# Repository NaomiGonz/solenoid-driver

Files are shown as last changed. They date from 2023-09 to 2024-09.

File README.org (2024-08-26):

** Single Channel Solenoid Driver

#+attr_org: :width 500px
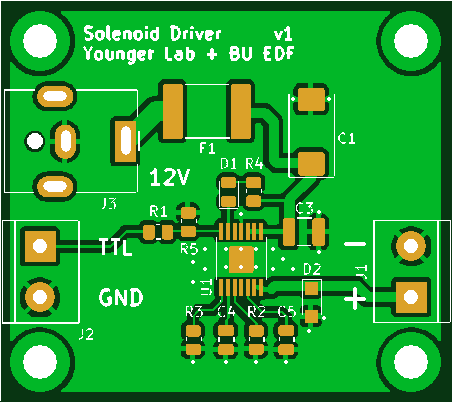
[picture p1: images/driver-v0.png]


A prototype single channel solenoid driver was developed for testing.

It is contained in the ~driver-v0~ folder.

We will have 3 manifolds with 8 of these in a row that need to be driven with 12V and signalled with a TTL line. All the manifolds will act in unison.

 - https://www.theleeco.com/product/lhd-series-2-way-control-solenoid-valve/
 - 3 boards, 8 channels each
 - 8 TTL inputs + GND
 - 8 12V outputs
 - 12V input on barrel jack
   - Plug:
     - https://www.digikey.com/en/products/detail/globtek-inc/CRP11856F00/16515770
     - Cable Assembly 2.1mm ID, 5.5mm OD Jack, Right Angle to Wire Leads Round 6.0' (1.83m)
   - Jack:
     - https://www.digikey.com/en/products/detail/cui-devices/PJ-063AH/2161208
     - PJ-063AH Power Barrel Connector Jack 2.10mm ID (0.083"), 5.50mm OD (0.217") Through Hole, Right Angle
 - LHDB1242115H
 - Spike+hold voltage: 12, 7.2
 - LOHM RATE** (Cv): 1500 Lohms (0.013)
 - Power Consumption At Hold Voltage (mW): 310
 - Response time: 10 ms Max

|----+-----------+-----+----------------------+--------------------+---------------------------|
|  # | Reference | Qty | Value                | PartNum            | Mfg                       |
|----+-----------+-----+----------------------+--------------------+---------------------------|
|  1 | C1        |   1 | 47uF                 | T491X476K035AT     | Kemet                     |
|  2 | C3        |   1 | 10uF                 | CL32A106KLULNNE    | Samsung Electro-Mechanics |
|  3 | C4        |   1 | 0.18 uF              | 08053C184KAT2A     | KYOCERA AVX               |
|  4 | C5        |   1 | 470pF                | C0805C471K5RAC7800 | Kemet                     |
|  5 | D1        |   1 | LED                  | 150080RS75000      | Wurth                     |
|  6 | D2        |   1 | PMEG10010ELRX        | PMEG10010ELRX      | Nexperia                  |
|  7 | F1        |   1 | 0ZCF0125FF2C         | 0ZCF0125FF2C       | Bel Fuse                  |
|  8 | J1, J2    |   2 | Screw_Terminal_01x02 | 282837-2           | TE                        |
|  9 | J3        |   1 | Barrel_Jack          | PJ-063AH           | CUI                       |
| 10 | R1        |   1 | 49R9                 | RC0805FR-0749R9L   | Yageo                     |
| 11 | R2        |   1 | 191k                 | RC0805FR-07191KL   | Yageo                     |
| 12 | R3        |   1 | 162k                 | RC0805FR-07162KL   | Yageo                     |
| 13 | R4, R5    |   2 | 4k7                  | RC0805JR-074K7L    | Yageo                     |
| 14 | U1        |   1 | DRV104PWP            | DRV104PWP          | TI                        |
|----+-----------+-----+----------------------+--------------------+---------------------------|

** Octal Channel Driver

** Dual Channel Complementary Driver

We will also have a pair of these valves that need to be driven by a single TTL
line in opposition (if one is in state A the other should be in state B).
 - LHDA1231415H
 - https://www.theleeco.com/product/lhd-series-3-way-control-solenoid-valve/
 - One TTL input  + GND
 - Two 12V complementary outputs

The solenoids should be driven with a high-side switch using a peak and hold circuit.

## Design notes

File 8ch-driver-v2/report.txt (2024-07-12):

Info: Processing symbol 'C1:Capacitor_Tantalum_SMD:CP_EIA-7343-43_Kemet-X_Pad2.25x2.55mm_HandSolder'.
Info: Processing symbol 'D39:LED_SMD:LED_0805_2012Metric'.
Info: Processing symbol 'C2:Capacitor_SMD:C_1210_3225Metric'.
Info: Processing symbol 'D10:Diode_SMD:Nexperia_CFP3_SOD-123W'.
Info: Processing symbol 'C3:Capacitor_SMD:C_1206_3216Metric'.
Info: Processing symbol 'Q2:Package_TO_SOT_SMD:SOT-23'.
Info: Processing symbol 'C4:Capacitor_SMD:C_1206_3216Metric'.
Info: Processing symbol 'D11:LED_SMD:LED_0805_2012Metric'.
Info: Processing symbol 'C5:Capacitor_SMD:C_1210_3225Metric'.
Info: Processing symbol 'D40:Diode_SMD:Nexperia_CFP3_SOD-123W'.
Info: Processing symbol 'C6:Capacitor_SMD:C_1206_3216Metric'.
Info: Processing symbol 'D12:LED_SMD:LED_0805_2012Metric'.
Info: Processing symbol 'C7:Capacitor_SMD:C_1206_3216Metric'.
Info: Processing symbol 'Q13:Package_TO_SOT_SMD:SOT-23'.
Info: Processing symbol 'C8:Capacitor_SMD:C_1210_3225Metric'.
Info: Processing symbol 'D13:Diode_SMD:Nexperia_CFP3_SOD-123W'.
Info: Processing symbol 'C9:Capacitor_SMD:C_1206_3216Metric'.
Info: Processing symbol 'D41:LED_SMD:LED_0805_2012Metric'.
Info: Processing symbol 'C10:Capacitor_SMD:C_1206_3216Metric'.
Info: Processing symbol 'D14:LED_SMD:LED_0805_2012Metric'.
Info: Processing symbol 'C11:Capacitor_SMD:C_1210_3225Metric'.
Info: Processing symbol 'Q3:Package_TO_SOT_SMD:SOT-23'.
Info: Processing symbol 'C12:Capacitor_SMD:C_1206_3216Metric'.
Info: Processing symbol 'D15:LED_SMD:LED_0805_2012Metric'.
Info: Processing symbol 'C13:Capacitor_SMD:C_1206_3216Metric'.
Info: Processing symbol 'D42:LED_SMD:LED_0805_2012Metric'.
Info: Processing symbol 'C14:Capacitor_SMD:C_1210_3225Metric'.
Info: Processing symbol 'D16:Diode_SMD:Nexperia_CFP3_SOD-123W'.
Info: Processing symbol 'C15:Capacitor_SMD:C_1206_3216Metric'.
Info: Processing symbol 'Q9:Package_TO_SOT_SMD:SOT-23'.
Info: Processing symbol 'C16:Capacitor_SMD:C_1206_3216Metric'.
Info: Processing symbol 'D17:LED_SMD:LED_0805_2012Metric'.
Info: Processing symbol 'C17:Capacitor_SMD:C_1210_3225Metric'.
Info: Processing symbol 'D43:Diode_SMD:Nexperia_CFP3_SOD-123W'.
Info: Processing symbol 'C18:Capacitor_SMD:C_1206_3216Metric'.
Info: Processing symbol 'D18:LED_SMD:LED_0805_2012Metric'.
Info: Processing symbol 'C19:Capacitor_SMD:C_1206_3216Metric'.
Info: Processing symbol 'Q4:Package_TO_SOT_SMD:SOT-23'.
Info: Processing symbol 'C20:Capacitor_SMD:C_1210_3225Metric'.
Info: Processing symbol 'D19:Diode_SMD:Nexperia_CFP3_SOD-123W'.
Info: Processing symbol 'C21:Capacitor_SMD:C_1206_3216Metric'.
Info: Processing symbol 'D44:LED_SMD:LED_0805_2012Metric'.
Info: Processing symbol 'C22:Capacitor_SMD:C_1206_3216Metric'.
Info: Processing symbol 'D20:LED_SMD:LED_0805_2012Metric'.
Info: Processing symbol 'C23:Capacitor_SMD:C_1210_3225Metric'.
Info: Processing symbol 'Q12:Package_TO_SOT_SMD:SOT-23'.
Info: Processing symbol 'C24:Capacitor_SMD:C_1206_3216Metric'.
Info: Processing symbol 'D21:LED_SMD:LED_0805_2012Metric'.
Info: Processing symbol 'C25:Capacitor_SMD:C_1206_3216Metric'.
Info: Processing symbol 'D45:LED_SMD:LED_0805_2012Metric'.
Info: Processing symbol 'C26:Capacitor_SMD:C_1210_3225Metric'.
Info: Processing symbol 'D22:Diode_SMD:Nexperia_CFP3_SOD-123W'.
Info: Processing symbol 'C27:Capacitor_SMD:C_1206_3216Metric'.
Info: Processing symbol 'Q5:Package_TO_SOT_SMD:SOT-23'.
Info: Processing symbol 'C28:Capacitor_SMD:C_1206_3216Metric'.
Info: Processing symbol 'D23:LED_SMD:LED_0805_2012Metric'.
Info: Processing symbol 'C29:Capacitor_SMD:C_1210_3225Metric'.
Info: Processing symbol 'D46:Diode_SMD:Nexperia_CFP3_SOD-123W'.
Info: Processing symbol 'C30:Capacitor_SMD:C_1206_3216Metric'.
Info: Processing symbol 'D24:LED_SMD:LED_0805_2012Metric'.
Info: Processing symbol 'C31:Capacitor_SMD:C_1206_3216Metric'.
Info: Processing symbol 'Q10:Package_TO_SOT_SMD:SOT-23'.
Info: Processing symbol 'C32:Capacitor_SMD:C_1210_3225Metric'.
Info: Processing symbol 'D25:Diode_SMD:Nexperia_CFP3_SOD-123W'.
Info: Processing symbol 'C33:Capacitor_SMD:C_1206_3216Metric'.
Info: Processing symbol 'D47:LED_SMD:LED_0805_2012Metric'.
Info: Processing symbol 'C34:Capacitor_SMD:C_1206_3216Metric'.
Info: Processing symbol 'D26:LED_SMD:LED_0805_2012Metric'.
Info: Processing symbol 'C35:Capacitor_SMD:C_1210_3225Metric'.
Info: Processing symbol 'Q6:Package_TO_SOT_SMD:SOT-23'.
Info: Processing symbol 'C36:Capacitor_SMD:C_1206_3216Metric'.
Info: Processing symbol 'D27:LED_SMD:LED_0805_2012Metric'.
Info: Processing symbol 'C37:Capacitor_SMD:C_1206_3216Metric'.
Info: Processing symbol 'D48:LED_SMD:LED_0805_2012Metric'.
Info: Processing symbol 'C38:Capacitor_SMD:C_1210_3225Metric'.
Info: Processing symbol 'D28:Diode_SMD:Nexperia_CFP3_SOD-123W'.
Info: Processing symbol 'C39:Capacitor_SMD:C_1206_3216Metric'.
Info: Processing symbol 'Q14:Package_TO_SOT_SMD:SOT-23'.
Info: Processing symbol 'C40:Capacitor_SMD:C_1206_3216Metric'.
Info: Processing symbol 'D29:LED_SMD:LED_0805_2012Metric'.
Info: Processing symbol 'C41:Capacitor_SMD:C_1210_3225Metric'.
Info: Processing symbol 'F1:Fuse:Fuse_2920_7451Metric'.
Info: Processing symbol 'C42:Capacitor_SMD:C_1206_3216Metric'.
Info: Processing symbol 'D30:LED_SMD:LED_0805_2012Metric'.
Info: Processing symbol 'C43:Capacitor_SMD:C_1206_3216Metric'.
Info: Processing symbol 'Q7:Package_TO_SOT_SMD:SOT-23'.
Info: Processing symbol 'C44:Capacitor_SMD:C_1210_3225Metric'.
Info: Processing symbol 'D31:Diode_SMD:Nexperia_CFP3_SOD-123W'.
Info: Processing symbol 'C45:Capacitor_SMD:C_1206_3216Metric'.
Info: Processing symbol 'H1:MountingHole:MountingHole_2.2mm_M2_Pad'.
Info: Processing symbol 'C46:Capacitor_SMD:C_1206_3216Metric'.
Info: Processing symbol 'D32:LED_SMD:LED_0805_2012Metric'.
Info: Processing symbol 'C47:Capacitor_SMD:C_1210_3225Metric'.
Info: Processing symbol 'Q16:Package_TO_SOT_SMD:SOT-23'.
Info: Processing symbol 'C48:Capacitor_SMD:C_1206_3216Metric'.
Info: Processing symbol 'D33:LED_SMD:LED_0805_2012Metric'.
Info: Processing symbol 'C49:Capacitor_SMD:C_1206_3216Metric'.
Info: Processing symbol 'H2:MountingHole:MountingHole_2.2mm_M2_Pad'.
Info: Processing symbol 'C50:Capacitor_SMD:C_1210_3225Metric'.
Info: Processing symbol 'D34:Diode_SMD:Nexperia_CFP3_SOD-123W'.
Info: Processing symbol 'C51:Capacitor_SMD:C_1210_3225Metric'.
Info: Processing symbol 'Q15:Package_TO_SOT_SMD:SOT-23'.
Info: Processing symbol 'D1:Diode_SMD:Nexperia_CFP3_SOD-123W'.
Info: Processing symbol 'D35:LED_SMD:LED_0805_2012Metric'.
Info: Processing symbol 'D2:LED_SMD:LED_0805_2012Metric'.
Info: Processing symbol 'J1:Connector_BarrelJack:BarrelJack_CUI_PJ-063AH_Horizontal'.
Info: Processing symbol 'D3:LED_SMD:LED_0805_2012Metric'.
Info: Processing symbol 'D36:LED_SMD:LED_0805_2012Metric'.
Info: Processing symbol 'D4:Diode_SMD:Nexperia_CFP3_SOD-123W'.
Info: Processing symbol 'Q11:Package_TO_SOT_SMD:SOT-23'.
Info: Processing symbol 'D5:LED_SMD:LED_0805_2012Metric'.
Info: Processing symbol 'D37:Diode_SMD:Nexperia_CFP3_SOD-123W'.
Info: Processing symbol 'D6:LED_SMD:LED_0805_2012Metric'.
Info: Processing symbol 'Q1:Package_TO_SOT_SMD:SOT-23'.
Info: Processing symbol 'D7:Diode_SMD:Nexperia_CFP3_SOD-123W'.
Info: Processing symbol 'D38:LED_SMD:LED_0805_2012Metric'.
Info: Processing symbol 'D8:LED_SMD:LED_0805_2012Metric'.
Info: Processing symbol 'Q8:Package_TO_SOT_SMD:SOT-23'.
Info: Processing symbol 'D9:LED_SMD:LED_0805_2012Metric'.
Info: Processing symbol 'R1:Resistor_SMD:R_1206_3216Metric'.
Info: Processing symbol 'R2:Resistor_SMD:R_1206_3216Metric'.
Info: Processing symbol 'R3:Resistor_SMD:R_1206_3216Metric'.
Info: Processing symbol 'R4:Resistor_SMD:R_1206_3216Metric'.
Info: Processing symbol 'R5:Resistor_SMD:R_1206_3216Metric'.
Info: Processing symbol 'R6:Resistor_SMD:R_1206_3216Metric'.
Info: Processing symbol 'R7:Resistor_SMD:R_1206_3216Metric'.
Info: Processing symbol 'R8:Resistor_SMD:R_1206_3216Metric'.
Info: Processing symbol 'R9:Resistor_SMD:R_1206_3216Metric'.
Info: Processing symbol 'R10:Resistor_SMD:R_1206_3216Metric'.
Info: Processing symbol 'R11:Resistor_SMD:R_1206_3216Metric'.
Info: Processing symbol 'R12:Resistor_SMD:R_1206_3216Metric'.
Info: Processing symbol 'R13:Resistor_SMD:R_1206_3216Metric'.
Info: Processing symbol 'R14:Resistor_SMD:R_1206_3216Metric'.
Info: Processing symbol 'R15:Resistor_SMD:R_1206_3216Metric'.
Info: Processing symbol 'R16:Resistor_SMD:R_1206_3216Metric'.
Info: Processing symbol 'R17:Resistor_SMD:R_1206_3216Metric'.
Info: Processing symbol 'R18:Resistor_SMD:R_1206_3216Metric'.
Info: Processing symbol 'R19:Resistor_SMD:R_1206_3216Metric'.
Info: Processing symbol 'R20:Resistor_SMD:R_1206_3216Metric'.
Info: Processing symbol 'R21:Resistor_SMD:R_1206_3216Metric'.
Info: Processing symbol 'R22:Resistor_SMD:R_1206_3216Metric'.
Info: Processing symbol 'R23:Resistor_SMD:R_1206_3216Metric'.
Info: Processing symbol 'R24:Resistor_SMD:R_1206_3216Metric'.
Info: Processing symbol 'R25:Resistor_SMD:R_1206_3216Metric'.
Info: Processing symbol 'R26:Resistor_SMD:R_1206_3216Metric'.
Info: Processing symbol 'R27:Resistor_SMD:R_1206_3216Metric'.
Info: Processing symbol 'R28:Resistor_SMD:R_1206_3216Metric'.
Info: Processing symbol 'R29:Resistor_SMD:R_1206_3216Metric'.
Info: Processing symbol 'R30:Resistor_SMD:R_1206_3216Metric'.
Info: Processing symbol 'R31:Resistor_SMD:R_1206_3216Metric'.
Info: Processing symbol 'R32:Resistor_SMD:R_1206_3216Metric'.
Info: Processing symbol 'R33:Resistor_SMD:R_1206_3216Metric'.
Info: Processing symbol 'R34:Resistor_SMD:R_1206_3216Metric'.
Info: Processing symbol 'R35:Resistor_SMD:R_1206_3216Metric'.
Info: Processing symbol 'R36:Resistor_SMD:R_1206_3216Metric'.
Info: Processing symbol 'R37:Resistor_SMD:R_1206_3216Metric'.
Info: Processing symbol 'R38:Resistor_SMD:R_1206_3216Metric'.
Info: Processing symbol 'R39:Resistor_SMD:R_1206_3216Metric'.
Info: Processing symbol 'R40:Resistor_SMD:R_1206_3216Metric'.
Info: Processing symbol 'R41:Resistor_SMD:R_1206_3216Metric'.
Info: Processing symbol 'R42:Resistor_SMD:R_1206_3216Metric'.
Info: Processing symbol 'R43:Resistor_SMD:R_1206_3216Metric'.
Info: Processing symbol 'R44:Resistor_SMD:R_1206_3216Metric'.
Info: Processing symbol 'R45:Resistor_SMD:R_1206_3216Metric'.
Info: Processing symbol 'R46:Resistor_SMD:R_1206_3216Metric'.
Info: Processing symbol 'R47:Resistor_SMD:R_1206_3216Metric'.
Info: Processing symbol 'R48:Resistor_SMD:R_1206_3216Metric'.
Info: Processing symbol 'R49:Resistor_SMD:R_1206_3216Metric'.
Info: Processing symbol 'R50:Resistor_SMD:R_1206_3216Metric'.
Info: Processing symbol 'R51:Resistor_SMD:R_1206_3216Metric'.
Info: Processing symbol 'R52:Resistor_SMD:R_1206_3216Metric'.
Info: Processing symbol 'R53:Resistor_SMD:R_1206_3216Metric'.
Info: Processing symbol 'R54:Resistor_SMD:R_1206_3216Metric'.
Info: Processing symbol 'R55:Resistor_SMD:R_1206_3216Metric'.
Info: Processing symbol 'R56:Resistor_SMD:R_1206_3216Metric'.
Info: Processing symbol 'R57:Resistor_SMD:R_1206_3216Metric'.
Info: Processing symbol 'R58:Resistor_SMD:R_1206_3216Metric'.
Info: Processing symbol 'R59:Resistor_SMD:R_1206_3216Metric'.
Info: Processing symbol 'R60:Resistor_SMD:R_1206_3216Metric'.
Info: Processing symbol 'R61:Resistor_SMD:R_1206_3216Metric'.
Info: Processing symbol 'R62:Resistor_SMD:R_1206_3216Metric'.
Info: Processing symbol 'R63:Resistor_SMD:R_1206_3216Metric'.
Info: Processing symbol 'R64:Resistor_SMD:R_1206_3216Metric'.
Info: Processing symbol 'R65:Resistor_SMD:R_1206_3216Metric'.
Info: Processing symbol 'R66:Resistor_SMD:R_1206_3216Metric'.
Info: Processing symbol 'R67:Resistor_SMD:R_1206_3216Metric'.
Info: Processing symbol 'R68:Resistor_SMD:R_1206_3216Metric'.
Info: Processing symbol 'R69:Resistor_SMD:R_1206_3216Metric'.
Info: Processing symbol 'R70:Resistor_SMD:R_1206_3216Metric'.
Info: Processing symbol 'R71:Resistor_SMD:R_1206_3216Metric'.
Info: Processing symbol 'R72:Resistor_SMD:R_1206_3216Metric'.
Info: Processing symbol 'R73:Resistor_SMD:R_1206_3216Metric'.
Info: Processing symbol 'R74:Resistor_SMD:R_1206_3216Metric'.
Info: Processing symbol 'R75:Resistor_SMD:R_1206_3216Metric'.
Info: Processing symbol 'R76:Resistor_SMD:R_1206_3216Metric'.
Info: Processing symbol 'R77:Resistor_SMD:R_1206_3216Metric'.
Info: Processing symbol 'R78:Resistor_SMD:R_1206_3216Metric'.
Info: Processing symbol 'R79:Resistor_SMD:R_1206_3216Metric'.
Info: Processing symbol 'R80:Resistor_SMD:R_1206_3216Metric'.
Info: Processing symbol 'R81:Resistor_SMD:R_1206_3216Metric'.
Info: Processing symbol 'R82:Resistor_SMD:R_1206_3216Metric'.
Info: Processing symbol 'R83:Resistor_SMD:R_1206_3216Metric'.
Info: Processing symbol 'R84:Resistor_SMD:R_1206_3216Metric'.
Info: Processing symbol 'R85:Resistor_SMD:R_1206_3216Metric'.
Info: Processing symbol 'R86:Resistor_SMD:R_1206_3216Metric'.
Info: Processing symbol 'R87:Resistor_SMD:R_1206_3216Metric'.
Info: Processing symbol 'R88:Resistor_SMD:R_1206_3216Metric'.
Info: Processing symbol 'R89:Resistor_SMD:R_1206_3216Metric'.
Info: Processing symbol 'R90:Resistor_SMD:R_1206_3216Metric'.
Info: Processing symbol 'R91:Resistor_SMD:R_1206_3216Metric'.
Info: Processing symbol 'R92:Resistor_SMD:R_1206_3216Metric'.
Info: Processing symbol 'R93:Resistor_SMD:R_1206_3216Metric'.
Info: Processing symbol 'R94:Resistor_SMD:R_1206_3216Metric'.
Info: Processing symbol 'R95:Resistor_SMD:R_1206_3216Metric'.
Info: Processing symbol 'R96:Resistor_SMD:R_1206_3216Metric'.
Info: Processing symbol 'U1:Solenoid_Driver:IC_TPS27S100BPWPR'.
Info: Processing symbol 'U2:Solenoid_Driver:IC_TPS27S100BPWPR'.
Info: Processing symbol 'U3:Solenoid_Driver:IC_TPS27S100BPWPR'.
Info: Processing symbol 'U4:Solenoid_Driver:IC_TPS27S100BPWPR'.
Info: Processing symbol 'U5:Solenoid_Driver:IC_TPS27S100BPWPR'.
Info: Processing symbol 'U6:Solenoid_Driver:IC_TPS27S100BPWPR'.
Info: Processing symbol 'U7:Solenoid_Driver:IC_TPS27S100BPWPR'.
Info: Processing symbol 'U8:Solenoid_Driver:IC_TPS27S100BPWPR'.
Info: Processing symbol 'U9:Solenoid_Driver:IC_TPS27S100BPWPR'.
Info: Processing symbol 'U10:Solenoid_Driver:IC_TPS27S100BPWPR'.
Info: Processing symbol 'U11:Solenoid_Driver:IC_TPS27S100BPWPR'.
Info: Processing symbol 'U12:Solenoid_Driver:IC_TPS27S100BPWPR'.
Info: Processing symbol 'U13:Solenoid_Driver:IC_TPS27S100BPWPR'.
Info: Processing symbol 'U14:Solenoid_Driver:IC_TPS27S100BPWPR'.
Info: Processing symbol 'U15:Solenoid_Driver:IC_TPS27S100BPWPR'.
Info: Processing symbol 'U16:Solenoid_Driver:IC_TPS27S100BPWPR'.
Info: Processing symbol 'U17:Package_TO_SOT_SMD:TO-252-2'.
Info: Processing symbol 'U18:FT4232H_FTD'.
Add Q14 (footprint 'Package_TO_SOT_SMD:SOT-23').
Add Q15 (footprint 'Package_TO_SOT_SMD:SOT-23').
Add Q16 (footprint 'Package_TO_SOT_SMD:SOT-23').
Add C1 (footprint 'Capacitor_Tantalum_SMD:CP_EIA-7343-43_Kemet-X_Pad2.25x2.55mm_HandSolder').
Add R1 (footprint 'Resistor_SMD:R_1206_3216Metric').
Add C2 (footprint 'Capacitor_SMD:C_1210_3225Metric').
Add R2 (footprint 'Resistor_SMD:R_1206_3216Metric').
Add C3 (footprint 'Capacitor_SMD:C_1206_3216Metric').
Add R3 (footprint 'Resistor_SMD:R_1206_3216Metric').
Add C4 (footprint 'Capacitor_SMD:C_1206_3216Metric').
Add R4 (footprint 'Resistor_SMD:R_1206_3216Metric').
Add C5 (footprint 'Capacitor_SMD:C_1210_3225Metric').
Add R5 (footprint 'Resistor_SMD:R_1206_3216Metric').
Add C6 (footprint 'Capacitor_SMD:C_1206_3216Metric').
Add R6 (footprint 'Resistor_SMD:R_1206_3216Metric').
Add C7 (footprint 'Capacitor_SMD:C_1206_3216Metric').
Add R7 (footprint 'Resistor_SMD:R_1206_3216Metric').
Add C8 (footprint 'Capacitor_SMD:C_1210_3225Metric').
Add R8 (footprint 'Resistor_SMD:R_1206_3216Metric').
Add C9 (footprint 'Capacitor_SMD:C_1206_3216Metric').
Add R9 (footprint 'Resistor_SMD:R_1206_3216Metric').
Add C10 (footprint 'Capacitor_SMD:C_1206_3216Metric').
Add R10 (footprint 'Resistor_SMD:R_1206_3216Metric').
Add C11 (footprint 'Capacitor_SMD:C_1210_3225Metric').
Add R11 (footprint 'Resistor_SMD:R_1206_3216Metric').
Add C12 (footprint 'Capacitor_SMD:C_1206_3216Metric').
Add R12 (footprint 'Resistor_SMD:R_1206_3216Metric').
Add C13 (footprint 'Capacitor_SMD:C_1206_3216Metric').
Add R13 (footprint 'Resistor_SMD:R_1206_3216Metric').
Add C14 (footprint 'Capacitor_SMD:C_1210_3225Metric').
Add R14 (footprint 'Resistor_SMD:R_1206_3216Metric').
Add C15 (footprint 'Capacitor_SMD:C_1206_3216Metric').
Add R15 (footprint 'Resistor_SMD:R_1206_3216Metric').
Add C16 (footprint 'Capacitor_SMD:C_1206_3216Metric').
Add R16 (footprint 'Resistor_SMD:R_1206_3216Metric').
Add C17 (footprint 'Capacitor_SMD:C_1210_3225Metric').
Add R17 (footprint 'Resistor_SMD:R_1206_3216Metric').
Add C18 (footprint 'Capacitor_SMD:C_1206_3216Metric').
Add R18 (footprint 'Resistor_SMD:R_1206_3216Metric').
Add C19 (footprint 'Capacitor_SMD:C_1206_3216Metric').
Add R19 (footprint 'Resistor_SMD:R_1206_3216Metric').
Add C20 (footprint 'Capacitor_SMD:C_1210_3225Metric').
Add R20 (footprint 'Resistor_SMD:R_1206_3216Metric').
Add C21 (footprint 'Capacitor_SMD:C_1206_3216Metric').
Add R21 (footprint 'Resistor_SMD:R_1206_3216Metric').
Add C22 (footprint 'Capacitor_SMD:C_1206_3216Metric').
Add R22 (footprint 'Resistor_SMD:R_1206_3216Metric').
Add C23 (footprint 'Capacitor_SMD:C_1210_3225Metric').
Add R23 (footprint 'Resistor_SMD:R_1206_3216Metric').
Add C24 (footprint 'Capacitor_SMD:C_1206_3216Metric').
Add R24 (footprint 'Resistor_SMD:R_1206_3216Metric').
Add C25 (footprint 'Capacitor_SMD:C_1206_3216Metric').
Add R25 (footprint 'Resistor_SMD:R_1206_3216Metric').
Add C26 (footprint 'Capacitor_SMD:C_1210_3225Metric').
Add R26 (footprint 'Resistor_SMD:R_1206_3216Metric').
Add C27 (footprint 'Capacitor_SMD:C_1206_3216Metric').
Add R27 (footprint 'Resistor_SMD:R_1206_3216Metric').
Add C28 (footprint 'Capacitor_SMD:C_1206_3216Metric').
Add R28 (footprint 'Resistor_SMD:R_1206_3216Metric').
Add C29 (footprint 'Capacitor_SMD:C_1210_3225Metric').
Add R29 (footprint 'Resistor_SMD:R_1206_3216Metric').
Add C30 (footprint 'Capacitor_SMD:C_1206_3216Metric').
Add R30 (footprint 'Resistor_SMD:R_1206_3216Metric').
Add C31 (footprint 'Capacitor_SMD:C_1206_3216Metric').
Add R31 (footprint 'Resistor_SMD:R_1206_3216Metric').
Add C32 (footprint 'Capacitor_SMD:C_1210_3225Metric').
Add R32 (footprint 'Resistor_SMD:R_1206_3216Metric').
Add C33 (footprint 'Capacitor_SMD:C_1206_3216Metric').
Add R33 (footprint 'Resistor_SMD:R_1206_3216Metric').
Add C34 (footprint 'Capacitor_SMD:C_1206_3216Metric').
Add R34 (footprint 'Resistor_SMD:R_1206_3216Metric').
Add C35 (footprint 'Capacitor_SMD:C_1210_3225Metric').
Add R35 (footprint 'Resistor_SMD:R_1206_3216Metric').
Add C36 (footprint 'Capacitor_SMD:C_1206_3216Metric').
Add R36 (footprint 'Resistor_SMD:R_1206_3216Metric').
Add C37 (footprint 'Capacitor_SMD:C_1206_3216Metric').
Add R37 (footprint 'Resistor_SMD:R_1206_3216Metric').
Add C38 (footprint 'Capacitor_SMD:C_1210_3225Metric').
Add R38 (footprint 'Resistor_SMD:R_1206_3216Metric').
Add C39 (footprint 'Capacitor_SMD:C_1206_3216Metric').
Add R39 (footprint 'Resistor_SMD:R_1206_3216Metric').
Add C40 (footprint 'Capacitor_SMD:C_1206_3216Metric').
Add R40 (footprint 'Resistor_SMD:R_1206_3216Metric').
Add C41 (footprint 'Capacitor_SMD:C_1210_3225Metric').
Add R41 (footprint 'Resistor_SMD:R_1206_3216Metric').
Add C42 (footprint 'Capacitor_SMD:C_1206_3216Metric').
Add R42 (footprint 'Resistor_SMD:R_1206_3216Metric').
Add C43 (footprint 'Capacitor_SMD:C_1206_3216Metric').
Add R43 (footprint 'Resistor_SMD:R_1206_3216Metric').
Add C44 (footprint 'Capacitor_SMD:C_1210_3225Metric').
Add R44 (footprint 'Resistor_SMD:R_1206_3216Metric').
Add C45 (footprint 'Capacitor_SMD:C_1206_3216Metric').
Add R45 (footprint 'Resistor_SMD:R_1206_3216Metric').
Add C46 (footprint 'Capacitor_SMD:C_1206_3216Metric').
Add R46 (footprint 'Resistor_SMD:R_1206_3216Metric').
Add C47 (footprint 'Capacitor_SMD:C_1210_3225Metric').
Add R47 (footprint 'Resistor_SMD:R_1206_3216Metric').
Add C48 (footprint 'Capacitor_SMD:C_1206_3216Metric').
Add R48 (footprint 'Resistor_SMD:R_1206_3216Metric').
Add C49 (footprint 'Capacitor_SMD:C_1206_3216Metric').
Add R49 (footprint 'Resistor_SMD:R_1206_3216Metric').
Add C50 (footprint 'Capacitor_SMD:C_1210_3225Metric').
Add R50 (footprint 'Resistor_SMD:R_1206_3216Metric').
Add C51 (footprint 'Capacitor_SMD:C_1210_3225Metric').
Add R51 (footprint 'Resistor_SMD:R_1206_3216Metric').
Add D1 (footprint 'Diode_SMD:Nexperia_CFP3_SOD-123W').
Add R52 (footprint 'Resistor_SMD:R_1206_3216Metric').
Add D2 (footprint 'LED_SMD:LED_0805_2012Metric').
Add R53 (footprint 'Resistor_SMD:R_1206_3216Metric').
Add D3 (footprint 'LED_SMD:LED_0805_2012Metric').
Add R54 (footprint 'Resistor_SMD:R_1206_3216Metric').
Add D4 (footprint 'Diode_SMD:Nexperia_CFP3_SOD-123W').
Add R55 (footprint 'Resistor_SMD:R_1206_3216Metric').
Add D5 (footprint 'LED_SMD:LED_0805_2012Metric').
Add R56 (footprint 'Resistor_SMD:R_1206_3216Metric').
Add D6 (footprint 'LED_SMD:LED_0805_2012Metric').
Add R57 (footprint 'Resistor_SMD:R_1206_3216Metric').
Add D7 (footprint 'Diode_SMD:Nexperia_CFP3_SOD-123W').
Add R58 (footprint 'Resistor_SMD:R_1206_3216Metric').
Add D8 (footprint 'LED_SMD:LED_0805_2012Metric').
Add R59 (footprint 'Resistor_SMD:R_1206_3216Metric').
Add D9 (footprint 'LED_SMD:LED_0805_2012Metric').
Add R60 (footprint 'Resistor_SMD:R_1206_3216Metric').
Add D10 (footprint 'Diode_SMD:Nexperia_CFP3_SOD-123W').
Add R61 (footprint 'Resistor_SMD:R_1206_3216Metric').
Add D11 (footprint 'LED_SMD:LED_0805_2012Metric').
Add R62 (footprint 'Resistor_SMD:R_1206_3216Metric').
Add D12 (footprint 'LED_SMD:LED_0805_2012Metric').
Add R63 (footprint 'Resistor_SMD:R_1206_3216Metric').
Add D13 (footprint 'Diode_SMD:Nexperia_CFP3_SOD-123W').
Add R64 (footprint 'Resistor_SMD:R_1206_3216Metric').
Add D14 (footprint 'LED_SMD:LED_0805_2012Metric').
Add R65 (footprint 'Resistor_SMD:R_1206_3216Metric').
Add D15 (footprint 'LED_SMD:LED_0805_2012Metric').
Add R66 (footprint 'Resistor_SMD:R_1206_3216Metric').
Add D16 (footprint 'Diode_SMD:Nexperia_CFP3_SOD-123W').
Add R67 (footprint 'Resistor_SMD:R_1206_3216Metric').
Add D17 (footprint 'LED_SMD:LED_0805_2012Metric').
Add R68 (footprint 'Resistor_SMD:R_1206_3216Metric').
Add D18 (footprint 'LED_SMD:LED_0805_2012Metric').
Add R69 (footprint 'Resistor_SMD:R_1206_3216Metric').
Add D19 (footprint 'Diode_SMD:Nexperia_CFP3_SOD-123W').
Add R70 (footprint 'Resistor_SMD:R_1206_3216Metric').
Add D20 (footprint 'LED_SMD:LED_0805_2012Metric').
Add R71 (footprint 'Resistor_SMD:R_1206_3216Metric').
Add D21 (footprint 'LED_SMD:LED_0805_2012Metric').
Add R72 (footprint 'Resistor_SMD:R_1206_3216Metric').
Add D22 (footprint 'Diode_SMD:Nexperia_CFP3_SOD-123W').
Add R73 (footprint 'Resistor_SMD:R_1206_3216Metric').
Add D23 (footprint 'LED_SMD:LED_0805_2012Metric').
Add R74 (footprint 'Resistor_SMD:R_1206_3216Metric').
Add D24 (footprint 'LED_SMD:LED_0805_2012Metric').
Add R75 (footprint 'Resistor_SMD:R_1206_3216Metric').
Add D25 (footprint 'Diode_SMD:Nexperia_CFP3_SOD-123W').
Add R76 (footprint 'Resistor_SMD:R_1206_3216Metric').
Add D26 (footprint 'LED_SMD:LED_0805_2012Metric').
Add R77 (footprint 'Resistor_SMD:R_1206_3216Metric').
Add D27 (footprint 'LED_SMD:LED_0805_2012Metric').
Add R78 (footprint 'Resistor_SMD:R_1206_3216Metric').
Add D28 (footprint 'Diode_SMD:Nexperia_CFP3_SOD-123W').
Add R79 (footprint 'Resistor_SMD:R_1206_3216Metric').
Add D29 (footprint 'LED_SMD:LED_0805_2012Metric').
Add R80 (footprint 'Resistor_SMD:R_1206_3216Metric').
Add D30 (footprint 'LED_SMD:LED_0805_2012Metric').
Add R81 (footprint 'Resistor_SMD:R_1206_3216Metric').
Add D31 (footprint 'Diode_SMD:Nexperia_CFP3_SOD-123W').
Add R82 (footprint 'Resistor_SMD:R_1206_3216Metric').
Add D32 (footprint 'LED_SMD:LED_0805_2012Metric').
Add R83 (footprint 'Resistor_SMD:R_1206_3216Metric').
Add D33 (footprint 'LED_SMD:LED_0805_2012Metric').
Add R84 (footprint 'Resistor_SMD:R_1206_3216Metric').
Add D34 (footprint 'Diode_SMD:Nexperia_CFP3_SOD-123W').
Add R85 (footprint 'Resistor_SMD:R_1206_3216Metric').
Add D35 (footprint 'LED_SMD:LED_0805_2012Metric').
Add R86 (footprint 'Resistor_SMD:R_1206_3216Metric').
Add D36 (footprint 'LED_SMD:LED_0805_2012Metric').
Add R87 (footprint 'Resistor_SMD:R_1206_3216Metric').
Add D37 (footprint 'Diode_SMD:Nexperia_CFP3_SOD-123W').
Add R88 (footprint 'Resistor_SMD:R_1206_3216Metric').
Add D38 (footprint 'LED_SMD:LED_0805_2012Metric').
Add R89 (footprint 'Resistor_SMD:R_1206_3216Metric').
Add D39 (footprint 'LED_SMD:LED_0805_2012Metric').
Add R90 (footprint 'Resistor_SMD:R_1206_3216Metric').
Add D40 (footprint 'Diode_SMD:Nexperia_CFP3_SOD-123W').
Add R91 (footprint 'Resistor_SMD:R_1206_3216Metric').
Add D41 (footprint 'LED_SMD:LED_0805_2012Metric').
Add R92 (footprint 'Resistor_SMD:R_1206_3216Metric').
Add D42 (footprint 'LED_SMD:LED_0805_2012Metric').
Add R93 (footprint 'Resistor_SMD:R_1206_3216Metric').
Add D43 (footprint 'Diode_SMD:Nexperia_CFP3_SOD-123W').
Add R94 (footprint 'Resistor_SMD:R_1206_3216Metric').
Add D44 (footprint 'LED_SMD:LED_0805_2012Metric').
Add R95 (footprint 'Resistor_SMD:R_1206_3216Metric').
Add D45 (footprint 'LED_SMD:LED_0805_2012Metric').
Add R96 (footprint 'Resistor_SMD:R_1206_3216Metric').
Add D46 (footprint 'Diode_SMD:Nexperia_CFP3_SOD-123W').
Add U1 (footprint 'Solenoid_Driver:IC_TPS27S100BPWPR').
Add D47 (footprint 'LED_SMD:LED_0805_2012Metric').
Add U2 (footprint 'Solenoid_Driver:IC_TPS27S100BPWPR').
Add D48 (footprint 'LED_SMD:LED_0805_2012Metric').
Add U3 (footprint 'Solenoid_Driver:IC_TPS27S100BPWPR').
Add F1 (footprint 'Fuse:Fuse_2920_7451Metric').
Add U4 (footprint 'Solenoid_Driver:IC_TPS27S100BPWPR').
Add J1 (footprint 'Connector_BarrelJack:BarrelJack_CUI_PJ-063AH_Horizontal').
Add U5 (footprint 'Solenoid_Driver:IC_TPS27S100BPWPR').
Add Q1 (footprint 'Package_TO_SOT_SMD:SOT-23').
Add U6 (footprint 'Solenoid_Driver:IC_TPS27S100BPWPR').
Add Q2 (footprint 'Package_TO_SOT_SMD:SOT-23').
Add U7 (footprint 'Solenoid_Driver:IC_TPS27S100BPWPR').
Add Q3 (footprint 'Package_TO_SOT_SMD:SOT-23').
Add U8 (footprint 'Solenoid_Driver:IC_TPS27S100BPWPR').
Add Q4 (footprint 'Package_TO_SOT_SMD:SOT-23').
Add U9 (footprint 'Solenoid_Driver:IC_TPS27S100BPWPR').
Add Q5 (footprint 'Package_TO_SOT_SMD:SOT-23').
Add U10 (footprint 'Solenoid_Driver:IC_TPS27S100BPWPR').
Add Q6 (footprint 'Package_TO_SOT_SMD:SOT-23').
Add U11 (footprint 'Solenoid_Driver:IC_TPS27S100BPWPR').
Add Q7 (footprint 'Package_TO_SOT_SMD:SOT-23').
Add U12 (footprint 'Solenoid_Driver:IC_TPS27S100BPWPR').
Add Q8 (footprint 'Package_TO_SOT_SMD:SOT-23').
Add U13 (footprint 'Solenoid_Driver:IC_TPS27S100BPWPR').
Add Q9 (footprint 'Package_TO_SOT_SMD:SOT-23').
Add U14 (footprint 'Solenoid_Driver:IC_TPS27S100BPWPR').
Add Q10 (footprint 'Package_TO_SOT_SMD:SOT-23').
Add U15 (footprint 'Solenoid_Driver:IC_TPS27S100BPWPR').
Add Q11 (footprint 'Package_TO_SOT_SMD:SOT-23').
Add U16 (footprint 'Solenoid_Driver:IC_TPS27S100BPWPR').
Add Q12 (footprint 'Package_TO_SOT_SMD:SOT-23').
Add U17 (footprint 'Package_TO_SOT_SMD:TO-252-2').
Add Q13 (footprint 'Package_TO_SOT_SMD:SOT-23').
Add U18 (footprint 'FT4232H_FTD').
Warning: No net found for component H1 pad 1 (no pin 1 in symbol).
Warning: No net found for component H2 pad 1 (no pin 1 in symbol).

Info: Total warnings: 2, errors: 0.

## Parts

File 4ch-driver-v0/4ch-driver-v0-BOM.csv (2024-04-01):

Source: | /Users/naomi_12/Desktop/Research/Younger-Lab/solenoid-driver-master/4ch-driver-v0/4ch-driver-v0.kicad_sch
Date: | 2024 March 31, Sunday 21:11:15
Tool: | Eeschema 7.0.7
Generator: | /Applications/KiCad/KiCad.app/Contents/SharedSupport/plugins/bom_csv_grouped_by_value.py
Component Count: | 68
Collated Components:
Item | Qty | Reference(s) | Value | LibPart | Footprint | Datasheet | DNP | Mfg | PartNum | Sim.Device | Sim.Pins
1 | 1 | C1 | 47uF | Device:C_Polarized | Capacitor_Tantalum_SMD:CP_EIA-7343-43_Kemet-X_Pad2.25x2.55mm_HandSolder | ~ |  | Kemet | T491X476K035AT
2 | 4 | C2, C7, C11, C14 | 0.18uF | Device:C_Small | Capacitor_SMD:C_0805_2012Metric | ~ |  | KYOCERA AVX | 08053C184KAT2A
3 | 4 | C3, C8, C12, C15 | 470pF | Device:C_Small | Capacitor_SMD:C_0805_2012Metric | ~ |  | Kemet | C0805C471K5RAC7800
4 | 4 | C4, C9, C13, C16 | 10uF | Device:C | Capacitor_SMD:C_1210_3225Metric | ~ |  | Samsung Electro-Mechanics | CL32A106KLULNNE
5 | 4 | C5, C10, C17, C18 | 0.1uF | Device:C_Small | Capacitor_SMD:C_0805_2012Metric | ~ |  | KYOCERA AVX | 08053C184KAT2A
6 | 1 | C6 | 10uF | Device:C_Small | Capacitor_SMD:C_1210_3225Metric | ~ |  | KYOCERA AVX | 08053C184KAT2A
7 | 8 | D1, D2, D4, D5, D7, D9, D11, D12 | LED | Device:LED | LED_SMD:LED_0805_2012Metric | ~ |  | Wurth | 150080RS75000
8 | 4 | D3, D6, D8, D10 | PMEG10010ELRX | Device:D | Diode_SMD:Nexperia_CFP3_SOD-123W | ~ |  | Nexperia | PMEG10010ELRX | D | 1=K 2=A
9 | 1 | F1 | 0ZCF0125FF2C | Device:Polyfuse | Fuse:Fuse_2920_7451Metric | ~ |  | Bel Fuse | 0ZCF0125FF2C
10 | 1 | J1 | Barrel_Jack | Connector:Barrel_Jack | Connector_BarrelJack:BarrelJack_CUI_PJ-063AH_Horizontal | ~ |  | CUI | PJ-063AH
11 | 2 | J2, J3 | Screw_Terminal_01x04 | Connector:Screw_Terminal_01x04 | TerminalBlock:TerminalBlock_bornier-4_P5.08mm | ~
12 | 1 | J4 | Screw_Terminal_01x02 | Connector:Screw_Terminal_01x02 | TerminalBlock:TerminalBlock_bornier-2_P5.08mm | ~ |  | TE | 282837-2
13 | 4 | Q1, Q2, Q3, Q4 | 2N7002E | Transistor_FET:2N7002E | Package_TO_SOT_SMD:SOT-23 | http://www.diodes.com/assets/Datasheets/ds30376.pdf
14 | 4 | R1, R2, R7, R21 | 1K | Device:R_US | Resistor_SMD:R_0805_2012Metric | ~ |  | Yageo | RC0805FR-07162KL
15 | 8 | R3, R4, R8, R9, R10, R13, R16, R17 | 4k7 | Device:R_US | Resistor_SMD:R_0805_2012Metric | ~ |  | Yageo | RC0805JR-074K7L
16 | 4 | R5, R11, R14, R18 | 162k | Device:R_US | Resistor_SMD:R_0805_2012Metric | ~ |  | Yageo | RC0805FR-07162KL
17 | 4 | R6, R12, R15, R19 | 191k | Device:R_US | Resistor_SMD:R_0805_2012Metric | ~ |  | Yageo | RC0805FR-07191KL
18 | 1 | R20 | 49R9 | Device:R_US | Resistor_SMD:R_0805_2012Metric | ~ |  | Yageo | RC0805FR-0749R9L
19 | 4 | U1, U3, U5, U6 | DRV104PWP | DRV104PWP:DRV104PWP | Solenoid_Driver:IC_TPS27S100BPWPR |  |  | TI | DRV104PWP
20 | 1 | U2 | BD750L2FP3-CE2 | Regulator_Linear:BD750L2FP3-CE | Package_TO_SOT_SMD:SOT-223-3_TabPin2
21 | 2 | U4, U7 | SN74LVC2G125DCUR | Buffer:SN74LVC2G125 | Package_SO:VSSOP-8_2.3x2mm_P0.5mm
22 | 1 | U8 | SN74AHCT1G04DBVR | Inverters:SN74AHCT1G04 | Package_TO_SOT_SMD:SOT-23-5

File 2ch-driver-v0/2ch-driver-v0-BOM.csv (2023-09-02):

Source: | /Users/naomi_12/Desktop/Meg-Younger-Lab/solenoid-driver-master/2ch-driver-v0/2ch-driver-v0.kicad_sch
Date: | 2023 August 22, Tuesday 11:58:14
Tool: | Eeschema 7.0.7
Generator: | /Applications/KiCad/KiCad.app/Contents/SharedSupport/plugins/bom_csv_grouped_by_value.py
Component Count: | 38
Collated Components:
Item | Qty Per Board | Reference(s) | Value | LibPart | Footprint | Link to Buy | Mfg | PartNum | Qty to Order | Indv Price | Group Price
1 | 1 | C1 | 47uF | Device:C_Polarized | Capacitor_Tantalum_SMD:CP_EIA-7343-43_Kemet-X_Pad2.25x2.55mm_HandSolder | https://www.digikey.com/en/products/detail/kemet/T491X476K035AT/818681 | Kemet | T491X476K035AT | 10 | $2.33 | $23.28
2 | 2 | C2, C7 | 0.18uF | Device:C_Small | Capacitor_SMD:C_0805_2012Metric | https://www.digikey.com/en/products/detail/kyocera-avx/08053C184KAT2A/563508 | KYOCERA AVX | 08053C184KAT2A | 50 | $0.14 | $4.32
3 | 2 | C3, C8 | 470pF | Device:C_Small | Capacitor_SMD:C_0805_2012Metric | https://www.digikey.com/en/products/detail/kemet/C0805C471K5RAC7800/411141 | Kemet | C0805C471K5RAC7800 | 50 | $0.04 | $1.87
4 | 3 | C4, C9,C6 | 10uF | Device:C | Capacitor_SMD:C_1210_3225Metric | https://www.digikey.com/en/products/detail/samsung-electro-mechanics/CL32A106KLULNNE/3888965 | Samsung Electro-Mechanics | CL32A106KLULNNE | 50 | $0.17 | $8.49
5 | 2 | C5, C10 | 0.1uF | Device:C_Small | Capacitor_SMD:C_0805_2012Metric | https://www.digikey.com/en/products/detail/samsung-electro-mechanics/CL21B104KBCNNNC/3886661 | Samsung Electro-Mechanics | CL21B104KBCNNNC | 50 | $0.02 | $1.20
6 | 2 | D2, D5 | LED Red | Device:LED | LED_SMD:LED_0805_2012Metric | https://www.digikey.com/en/products/detail/wŸrth-elektronik/150080RS75000/4489918 | Wurth | 150080RS75000 | 50 | $0.18 | $8.80
7 | 2 | D1, D4 | LED Green | Device:LED | LED_SMD:LED_0805_2012Metric | https://www.digikey.com/en/products/detail/wŸrth-elektronik/150080VS75000/4489924 | Wurth | 150080VS75000 | 50 | $0.18 | $8.80
8 | 2 | D3, D6 | PMEG10010ELRX | Device:D | Diode_SMD:Nexperia_CFP3_SOD-123W | https://www.digikey.com/en/products/detail/nexperia-usa-inc/PMEG10010ELRX/5436248 | Nexperia | PMEG10010ELRX | 50 | $0.29 | $14.30
9 | 1 | F1 | 0ZCF0125FF2C | Device:Polyfuse | Fuse:Fuse_2920_7451Metric | https://www.digikey.com/en/products/detail/bel-fuse-inc/0ZCF0125FF2C/4156315 | Bel Fuse | 0ZCF0125FF2C | 10 | $0.28 | $2.84
10 | 1 | J1 | Barrel_Jack | Connector:Barrel_Jack | Connector_BarrelJack:BarrelJack_CUI_PJ-063AH_Horizontal | https://www.digikey.com/en/products/detail/cui-devices/PJ-063AH/2161208 | CUI | PJ-063AH | 25 | $1.27 | $31.85
11 | 3 | J2, J3, J5 | Screw_Terminal_01x02 | Connector:Screw_Terminal_01x02 | TerminalBlock:TerminalBlock_bornier-2_P5.08mm | https://www.digikey.com/en/products/detail/te-connectivity-amp-connectors/282837-2/2187973 | TE | 282837-2 | 25 | $0.68 | $16.95
12 | 2 | Q1, Q2 | 2N7002E | Transistor_FET:2N7002E | Package_TO_SOT_SMD:SOT-23 | https://www.digikey.com/en/products/detail/diodes-incorporated/ZXMN2B01FTA/1557727 | Diodes Inc | ZXMN2B01FTA | 10 | $0.37 | $3.74
13 | 2 | R1, R7 | 1K | Device:R_US | Resistor_SMD:R_0805_2012Metric | https://www.digikey.com/en/products/detail/yageo/RC0805FR-071KL/727444 | Yageo | RC0805FR-071KL | 50 | $0.02 | $0.76
14 | 1 | R2 | 49R9 | Device:R_US | Resistor_SMD:R_0805_2012Metric | https://www.digikey.com/en/products/detail/yageo/RC0805FR-0749R9L/727984 | Yageo | RC0805FR-0749R9L | 10 | $0.02 | $0.24
15 | 4 | R3, R4, R9, R10 | 4k7 | Device:R_US | Resistor_SMD:R_0805_2012Metric | https://www.digikey.com/en/products/detail/yageo/RC0805JR-074K7L/728327 | Yageo | RC0805JR-074K7L | 50 | $0.01 | $0.68
16 | 2 | R5, R11 | 162k | Device:R_US | Resistor_SMD:R_0805_2012Metric | https://www.digikey.com/en/products/detail/yageo/RC0805FR-07162KL/727630 | Yageo | RC0805FR-07162KL | 50 | $0.02 | $0.76
17 | 2 | R6, R12 | 191k | Device:R_US | Resistor_SMD:R_0805_2012Metric | https://www.digikey.com/en/products/detail/yageo/RC0805FR-07191KL/727660 | Yageo | RC0805FR-07191KL | 50 | $0.02 | $0.77
18 | 2 | U1, U3 | DRV104PWP | DRV104PWP:DRV104PWP | Solenoid_Driver:IC_TPS27S100BPWPR | https://www.digikey.com/en/products/detail/texas-instruments/DRV104PWP/1509554 | TI | DRV104PWP | 25 | $4.55 | $113.74
19 | 1 | U2 | ~ | Regulator_Linear:BD750L2FP3-CE | Package_TO_SOT_SMD:SOT-223-3_TabPin2 | https://www.digikey.com/en/products/detail/rohm-semiconductor/BD750L2FP3-CE2/4625570 | Rohm | BD750L2FP3-CE2 | 10 | $1.54 | $15.39
20 | 1 | U4 | ~ | Inverters:SN74AHCT1G04 | Package_TO_SOT_SMD:SOT-23-5 | https://www.digikey.com/en/products/detail/texas-instruments/SN74AHCT1G04DBVR/276756 | Texas Instr | SN74AHCT1G04DBVR | 10 | $0.27 | $2.69
 |  |  |  |  |  |  |  |  |  | TOTAL: | $261.47
 | Digikey Cart: | https://www.digikey.com/short/47vpb32n

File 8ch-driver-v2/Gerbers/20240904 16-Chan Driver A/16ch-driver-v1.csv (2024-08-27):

Id | Designator | Footprint | Quantity | Designation | Supplier and ref
1 | R23,R11,R35,R29,R47,R5,R17,R41,R59,R71,R77,R65,R89,R95,R83,R53 | R_1206_3216Metric | 16 | 191k
2 | C3,C6,C18,C12,C24,C9,C21,C15,C27,C39,C30,C45,C42,C36,C33,C48 | C_1206_3216Metric | 16 | 0.18uF
3 | R16,R40,R37,R19,R28,R48,R4,R46,R30,R1,R34,R43,R10,R6,R7,R18,R24,R13,R42,R12,R31,R22,R36,R25,R78,R55,R67,R60,R70,R76,R90,R61,R94,R85,R64,R84,R54,R49,R73,R72,R66,R96,R91,R58,R52,R82,R79,R88 | R_1206_3216Metric | 48 | 4k7
4 | C23,C11,C14,C17,C2,C20,C5,C8,C38,C32,C35,C29,C26,C41,C47,C44 | C_1210_3225Metric | 16 | 10uF
5 | D33,D42,D39,D24,D27,D45,D3,D9,D30,D18,D15,D21,D48,D36,D12,D6 | LED_0805_2012Metric | 16 | LED
6 | C4,C16,C13,C19,C7,C25,C22,C10,C49,C40,C37,C31,C43,C46,C34,C28 | C_1206_3216Metric | 16 | 470pF
7 | D38,D29,D5,D41,D11,D26,D23,D47,D44,D20,D2,D14,D8,D32,D35,D17 | LED_0805_2012Metric | 16 | LED Green
8 | H3,H1,H2,H4 | MountingHole_3.2mm_M3 | 4 | MountingHole
9 | R3,R9,R33,R45,R39,R15,R27,R21,R57,R63,R69,R75,R93,R51,R81,R87 | R_1206_3216Metric | 16 | 49R9
10 | U3,U8,U1,U2,U5,U4,U6,U7,U12,U13,U9,U16,U10,U14,U15,U11 | IC_TPS27S100BPWPR | 16 | DRV104PWP
11 | D13,D22,D7,D10,D4,D16,D19,D1,D28,D25,D37,D34,D40,D43,D46,D31 | Nexperia_CFP3_SOD-123W | 16 | PMEG10010ELRX
12 | LP4,LP7,LP5,LP8,LP2,LP6,LP1,LP3 | Lightpipe_LPF-C014301S | 8 | LPF-C014301S
13 | C1 | CP_EIA-7343-43_Kemet-X_Pad2.25x2.55mm_HandSolder | 1 | 47uF
14 | J3,J4 | CUI_TBL009-254-16GY-2GY | 2 | TBL009-254-16GY-2GY
15 | Q6,Q2,Q7,Q4,Q3,Q1,Q8,Q5,Q9,Q16,Q15,Q10,Q11,Q14,Q12,Q13 | SOT-23 | 16 | 2N7002E
16 | R14,R8,R44,R38,R20,R32,R2,R26,R92,R74,R62,R68,R50,R80,R56,R86 | R_1206_3216Metric | 16 | 162k
17 | F1 | Fuse_2920_7451Metric | 1 | 0ZCF0125FF2C
18 | J1 | CUI_PJ-063AH | 1 | PJ-063AH
19 | U18 | FT4232H_MINI_MODULE | 1 | FT4232H MINI MODULE

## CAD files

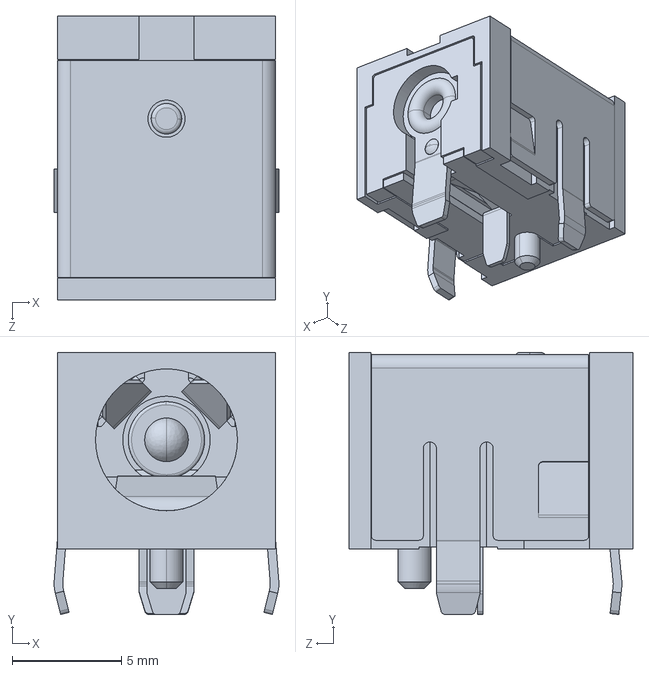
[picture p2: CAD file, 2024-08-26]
8ch-driver-v2/step/CUI_DEVICES_PJ-063AH.step
10.3 x 12.0 x 13.0 mm

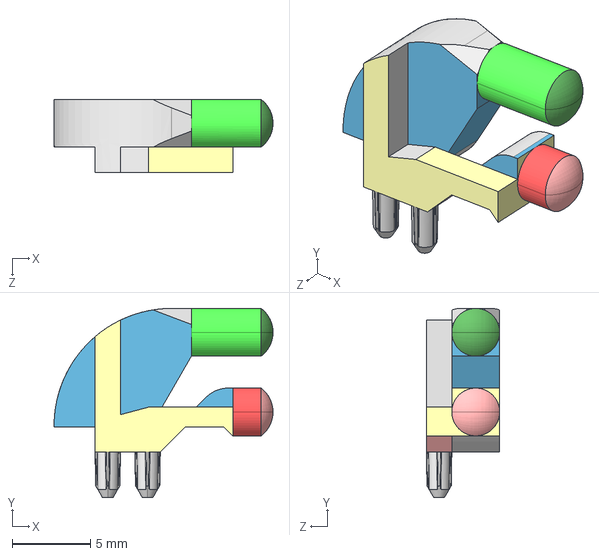
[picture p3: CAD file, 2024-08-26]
8ch-driver-v2/step/LP-230.IGS
14.0 x 12.1 x 4.67 mm

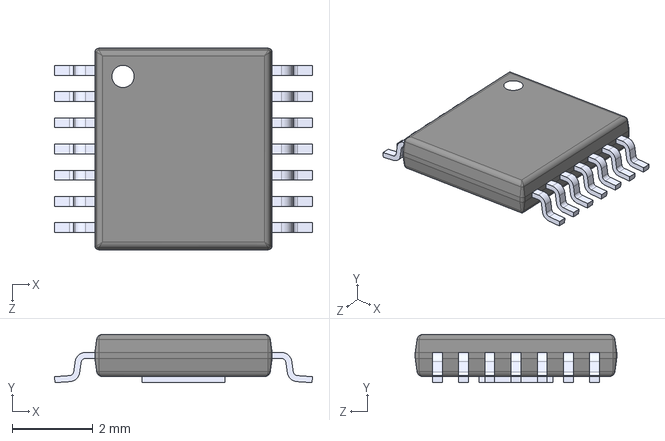
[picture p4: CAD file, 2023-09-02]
8ch-driver-v2/step/DRV104PWP.step
6.40 x 1.20 x 5.00 mm

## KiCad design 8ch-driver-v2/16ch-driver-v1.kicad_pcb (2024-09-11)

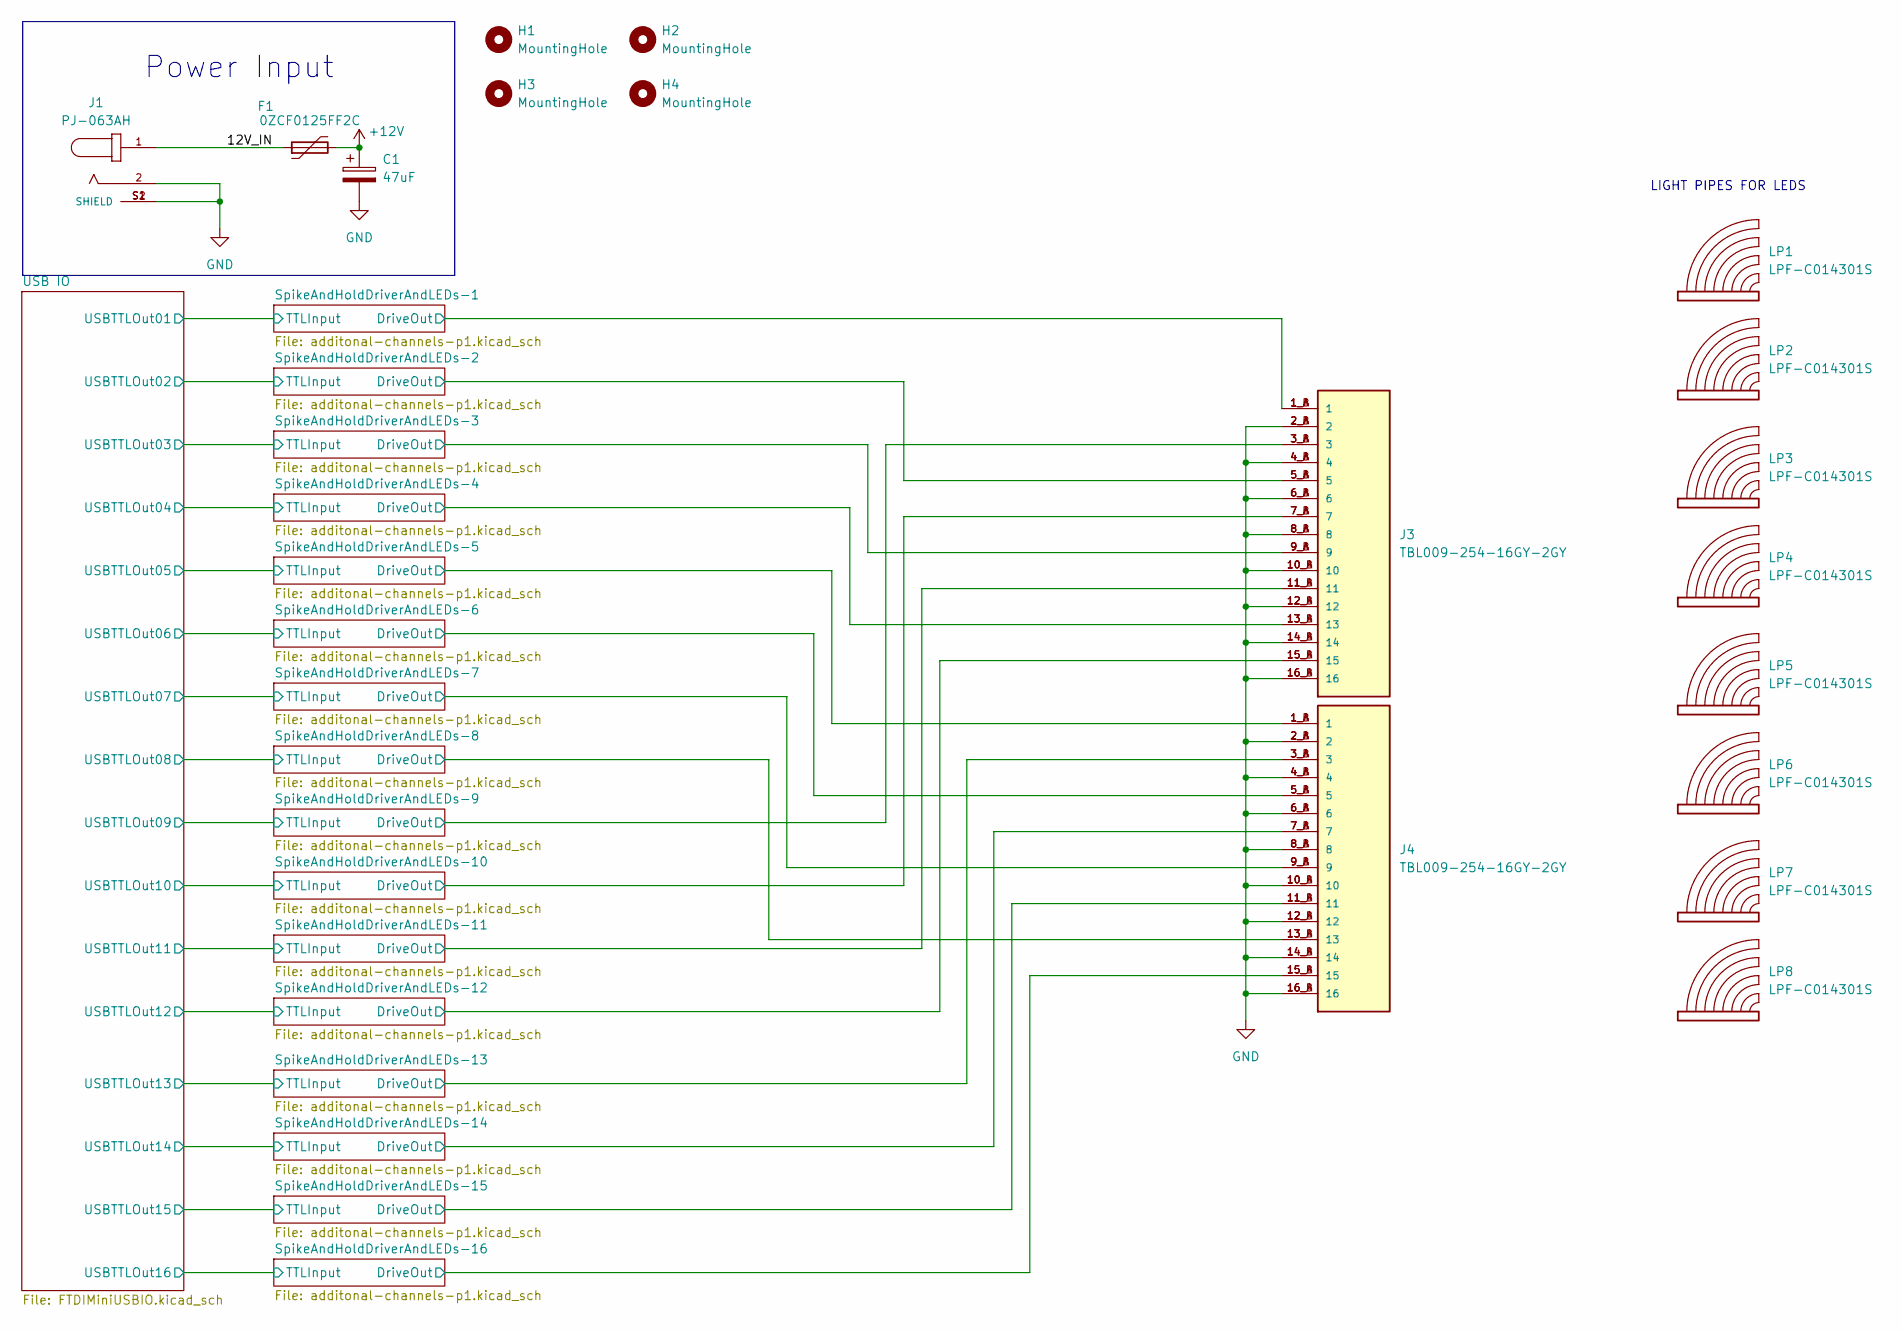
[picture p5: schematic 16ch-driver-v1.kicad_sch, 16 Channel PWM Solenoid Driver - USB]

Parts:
C1: 47uF; CP_EIA-7343-43_Kemet-X_Pad2.25x2.55mm_HandSolder; PartNum T491X476K035AT
F1: 0ZCF0125FF2C; Fuse_2920_7451Metric; PartNum 0ZCF0125FF2C
H1, H2, H3, H4: MountingHole; MountingHole_3.2mm_M3
J1: PJ-063AH; CUI_PJ-063AH; PARTREV 1.02
J3, J4: TBL009-254-16GY-2GY; CUI_TBL009-254-16GY-2GY
LP1, LP2, LP3, LP4, LP5, LP6, LP7, LP8: LPF-C014301S; Lightpipe_LPF-C014301S

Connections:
+12V: C1.1, F1.2; also elsewhere on the board
/12V_IN: F1.1, J1.1
/SpikeAndHoldDriverAndLEDs-1/DriveOut: J3.1_A (1), J3.1_B (1); also elsewhere on the board
/SpikeAndHoldDriverAndLEDs-2/DriveOut: J3.5_A (5), J3.5_B (5); also elsewhere on the board
/SpikeAndHoldDriverAndLEDs-3/DriveOut: J3.9_A (9), J3.9_B (9); also elsewhere on the board
/SpikeAndHoldDriverAndLEDs-4/DriveOut: J3.13_A (13), J3.13_B (13); also elsewhere on the board
/SpikeAndHoldDriverAndLEDs-5/DriveOut: J4.1_A (1), J4.1_B (1); also elsewhere on the board
/SpikeAndHoldDriverAndLEDs-6/DriveOut: J4.5_A (5), J4.5_B (5); also elsewhere on the board
/SpikeAndHoldDriverAndLEDs-7/DriveOut: J4.9_A (9), J4.9_B (9); also elsewhere on the board
/SpikeAndHoldDriverAndLEDs-8/DriveOut: J4.13_A (13), J4.13_B (13); also elsewhere on the board
/SpikeAndHoldDriverAndLEDs-9/DriveOut: J3.3_A (3), J3.3_B (3); also elsewhere on the board
/SpikeAndHoldDriverAndLEDs-10/DriveOut: J3.7_A (7), J3.7_B (7); also elsewhere on the board
/SpikeAndHoldDriverAndLEDs-11/DriveOut: J3.11_A (11), J3.11_B (11); also elsewhere on the board
/SpikeAndHoldDriverAndLEDs-12/DriveOut: J3.15_A (15), J3.15_B (15); also elsewhere on the board
/SpikeAndHoldDriverAndLEDs-13/DriveOut: J4.3_A (3), J4.3_B (3); also elsewhere on the board
/SpikeAndHoldDriverAndLEDs-14/DriveOut: J4.7_A (7), J4.7_B (7); also elsewhere on the board
/SpikeAndHoldDriverAndLEDs-15/DriveOut: J4.11_A (11), J4.11_B (11); also elsewhere on the board
/SpikeAndHoldDriverAndLEDs-16/DriveOut: J4.15_A (15), J4.15_B (15); also elsewhere on the board
GND: C1.2, J1.2, J1.S1 (SHIELD), J1.S2 (SHIELD), J3.2_A (2), J3.2_B (2), J3.4_A (4), J3.4_B (4), J3.6_A (6), J3.6_B (6), J3.8_A (8), J3.8_B (8), J3.10_A (10), J3.10_B (10), J3.12_A (12), J3.12_B (12), J3.14_A (14), J3.14_B (14), J3.16_A (16), J3.16_B (16), J4.2_A (2), J4.2_B (2), J4.4_A (4), J4.4_B (4), J4.6_A (6), J4.6_B (6), J4.8_A (8), J4.8_B (8), J4.10_A (10), J4.10_B (10), J4.12_A (12), J4.12_B (12), J4.14_A (14), J4.14_B (14), J4.16_A (16), J4.16_B (16); also elsewhere on the board

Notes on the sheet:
Power Input
LIGHT PIPES FOR LEDS

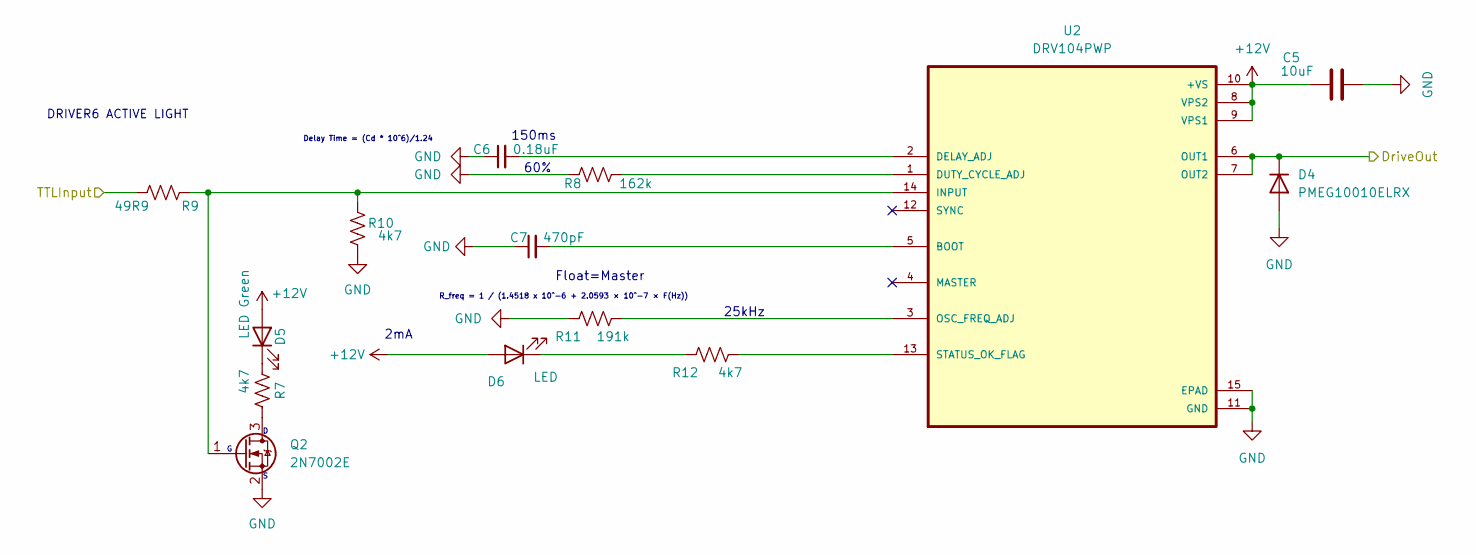
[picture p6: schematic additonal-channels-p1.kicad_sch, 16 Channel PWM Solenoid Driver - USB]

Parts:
C5: 10uF; C_1210_3225Metric; PartNum CL32A106KLULNNE
C6: 0.18uF; C_1206_3216Metric; PartNum 08053C184KAT2A
C7: 470pF; C_1206_3216Metric; PartNum C0805C471K5RAC7800
D4: PMEG10010ELRX; Nexperia_CFP3_SOD-123W; PartNum PMEG10010ELRX
D5: LED Green; LED_0805_2012Metric; PartNum 150080RS75000
D6: LED; LED_0805_2012Metric; PartNum 150080RS75000
Q2: 2N7002E; SOT-23
R7: 4k7; R_1206_3216Metric; PartNum RC0805FR-07162KL
R8: 162k; R_1206_3216Metric; PartNum RC0805FR-07162KL
R9: 49R9; R_1206_3216Metric; PartNum RC0805FR-0749R9L
R10, R12: 4k7; R_1206_3216Metric; PartNum RC0805JR-074K7L
R11: 191k; R_1206_3216Metric; PartNum RC0805FR-07191KL
U2: DRV104PWP; IC_TPS27S100BPWPR; PartNum DRV104PWP

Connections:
+12V: C5.1, D5.2 (A), D6.2 (A), U2.8 (VPS2), U2.9 (VPS1), U2.10 (+VS); also elsewhere on the board
/SpikeAndHoldDriverAndLEDs-2/DriveOut: D4.1 (K), U2.6 (OUT1), U2.7 (OUT2); also elsewhere on the board
/SpikeAndHoldDriverAndLEDs-2/TTLInput: R9.1; also elsewhere on the board
GND: C5.2, C6.1, C7.1, D4.2 (A), Q2.2 (S), R8.1, R10.1, R11.1, U2.11 (GND), U2.15 (EPAD); also elsewhere on the board
unnamed: D5.1 (K), R7.1
unnamed: D6.1 (K), R12.1
unnamed: Q2.3 (D), R7.2
unnamed: Q2.1 (G), R9.2, R10.2, U2.14 (INPUT)
unnamed: C7.2, U2.5 (BOOT)
unnamed: C6.2, U2.2 (DELAY_ADJ)
unnamed: R8.2, U2.1 (DUTY_CYCLE_ADJ)
unnamed: R11.2, U2.3 (OSC_FREQ_ADJ)
unnamed: R12.2, U2.13 (STATUS_OK_FLAG)

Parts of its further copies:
C2, C8, C11, C14, C17, C20, C23, C26, C29, C32, C35, C38, C41, C44, C47: 10uF; C_1210_3225Metric; PartNum CL32A106KLULNNE
C3, C9, C12, C15, C18, C21, C24, C27, C30, C33, C36, C39, C42, C45, C48: 0.18uF; C_1206_3216Metric; PartNum 08053C184KAT2A
C4, C10, C13, C16, C19, C22, C25, C28, C31, C34, C37, C40, C43, C46, C49: 470pF; C_1206_3216Metric; PartNum C0805C471K5RAC7800
D1, D7, D10, D13, D16, D19, D22, D25, D28, D31, D34, D37, D40, D43, D46: PMEG10010ELRX; Nexperia_CFP3_SOD-123W; PartNum PMEG10010ELRX
D2, D8, D11, D14, D17, D20, D23, D26, D29, D32, D35, D38, D41, D44, D47: LED Green; LED_0805_2012Metric; PartNum 150080RS75000
D3, D9, D12, D15, D18, D21, D24, D27, D30, D33, D36, D39, D42, D45, D48: LED; LED_0805_2012Metric; PartNum 150080RS75000
Q1, Q3, Q4, Q5, Q6, Q7, Q8, Q9, Q10, Q11, Q12, Q13, Q14, Q15, Q16: 2N7002E; SOT-23
R1, R13, R19, R25, R31, R37, R43, R49, R55, R61, R67, R73, R79, R85, R91: 4k7; R_1206_3216Metric; PartNum RC0805FR-07162KL
R2, R14, R20, R26, R32, R38, R44, R50, R56, R62, R68, R74, R80, R86, R92: 162k; R_1206_3216Metric; PartNum RC0805FR-07162KL
R3, R15, R21, R27, R33, R39, R45, R51, R57, R63, R69, R75, R81, R87, R93: 49R9; R_1206_3216Metric; PartNum RC0805FR-0749R9L
R4, R6, R16, R18, R22, R24, R28, R30, R34, R36, R40, R42, R46, R48, R52, R54, R58, R60, R64, R66, R70, R72, R76, R78, R82, R84, R88, R90, R94, R96: 4k7; R_1206_3216Metric; PartNum RC0805JR-074K7L
R5, R17, R23, R29, R35, R41, R47, R53, R59, R65, R71, R77, R83, R89, R95: 191k; R_1206_3216Metric; PartNum RC0805FR-07191KL
U1, U3, U4, U5, U6, U7, U8, U9, U10, U11, U12, U13, U14, U15, U16: DRV104PWP; IC_TPS27S100BPWPR; PartNum DRV104PWP

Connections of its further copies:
+12V: C2.1, C8.1, C11.1, C14.1, C17.1, C20.1, C23.1, C26.1, C29.1, C32.1, C35.1, C38.1, C41.1, C44.1, C47.1, D2.2 (A), D3.2 (A), D8.2 (A), D9.2 (A), D11.2 (A), D12.2 (A), D14.2 (A), D15.2 (A), D17.2 (A), D18.2 (A), D20.2 (A), D21.2 (A), D23.2 (A), D24.2 (A), D26.2 (A), D27.2 (A), D29.2 (A), D30.2 (A), D32.2 (A), D33.2 (A), D35.2 (A), D36.2 (A), D38.2 (A), D39.2 (A), D41.2 (A), D42.2 (A), D44.2 (A), D45.2 (A), D47.2 (A), D48.2 (A), U1.8 (VPS2), U1.9 (VPS1), U1.10 (+VS), U3.8 (VPS2), U3.9 (VPS1), U3.10 (+VS), U4.8 (VPS2), U4.9 (VPS1), U4.10 (+VS), U5.8 (VPS2), U5.9 (VPS1), U5.10 (+VS), U6.8 (VPS2), U6.9 (VPS1), U6.10 (+VS), U7.8 (VPS2), U7.9 (VPS1), U7.10 (+VS), U8.8 (VPS2), U8.9 (VPS1), U8.10 (+VS), U9.8 (VPS2), U9.9 (VPS1), U9.10 (+VS), U10.8 (VPS2), U10.9 (VPS1), U10.10 (+VS), U11.8 (VPS2), U11.9 (VPS1), U11.10 (+VS), U12.8 (VPS2), U12.9 (VPS1), U12.10 (+VS), U13.8 (VPS2), U13.9 (VPS1), U13.10 (+VS), U14.8 (VPS2), U14.9 (VPS1), U14.10 (+VS), U15.8 (VPS2), U15.9 (VPS1), U15.10 (+VS), U16.8 (VPS2), U16.9 (VPS1), U16.10 (+VS); also elsewhere on the board
/SpikeAndHoldDriverAndLEDs-1/DriveOut: D1.1 (K), U1.6 (OUT1), U1.7 (OUT2); also elsewhere on the board
/SpikeAndHoldDriverAndLEDs-1/TTLInput: R3.1; also elsewhere on the board
/SpikeAndHoldDriverAndLEDs-3/DriveOut: D7.1 (K), U3.6 (OUT1), U3.7 (OUT2); also elsewhere on the board
/SpikeAndHoldDriverAndLEDs-3/TTLInput: R15.1; also elsewhere on the board
/SpikeAndHoldDriverAndLEDs-4/DriveOut: D10.1 (K), U4.6 (OUT1), U4.7 (OUT2); also elsewhere on the board
/SpikeAndHoldDriverAndLEDs-4/TTLInput: R21.1; also elsewhere on the board
/SpikeAndHoldDriverAndLEDs-5/DriveOut: D13.1 (K), U5.6 (OUT1), U5.7 (OUT2); also elsewhere on the board
/SpikeAndHoldDriverAndLEDs-5/TTLInput: R27.1; also elsewhere on the board
/SpikeAndHoldDriverAndLEDs-6/DriveOut: D16.1 (K), U6.6 (OUT1), U6.7 (OUT2); also elsewhere on the board
/SpikeAndHoldDriverAndLEDs-6/TTLInput: R33.1; also elsewhere on the board
/SpikeAndHoldDriverAndLEDs-7/DriveOut: D19.1 (K), U7.6 (OUT1), U7.7 (OUT2); also elsewhere on the board
/SpikeAndHoldDriverAndLEDs-7/TTLInput: R39.1; also elsewhere on the board
/SpikeAndHoldDriverAndLEDs-8/DriveOut: D22.1 (K), U8.6 (OUT1), U8.7 (OUT2); also elsewhere on the board
/SpikeAndHoldDriverAndLEDs-8/TTLInput: R45.1; also elsewhere on the board
/SpikeAndHoldDriverAndLEDs-9/DriveOut: D25.1 (K), U9.6 (OUT1), U9.7 (OUT2); also elsewhere on the board
/SpikeAndHoldDriverAndLEDs-9/TTLInput: R51.1; also elsewhere on the board
/SpikeAndHoldDriverAndLEDs-10/DriveOut: D28.1 (K), U10.6 (OUT1), U10.7 (OUT2); also elsewhere on the board
/SpikeAndHoldDriverAndLEDs-10/TTLInput: R57.1; also elsewhere on the board
/SpikeAndHoldDriverAndLEDs-11/DriveOut: D31.1 (K), U11.6 (OUT1), U11.7 (OUT2); also elsewhere on the board
/SpikeAndHoldDriverAndLEDs-11/TTLInput: R63.1; also elsewhere on the board
/SpikeAndHoldDriverAndLEDs-12/DriveOut: D34.1 (K), U12.6 (OUT1), U12.7 (OUT2); also elsewhere on the board
/SpikeAndHoldDriverAndLEDs-12/TTLInput: R69.1; also elsewhere on the board
/SpikeAndHoldDriverAndLEDs-13/DriveOut: D37.1 (K), U13.6 (OUT1), U13.7 (OUT2); also elsewhere on the board
/SpikeAndHoldDriverAndLEDs-13/TTLInput: R75.1; also elsewhere on the board
/SpikeAndHoldDriverAndLEDs-14/DriveOut: D40.1 (K), U14.6 (OUT1), U14.7 (OUT2); also elsewhere on the board
/SpikeAndHoldDriverAndLEDs-14/TTLInput: R81.1; also elsewhere on the board
/SpikeAndHoldDriverAndLEDs-15/DriveOut: D43.1 (K), U15.6 (OUT1), U15.7 (OUT2); also elsewhere on the board
/SpikeAndHoldDriverAndLEDs-15/TTLInput: R87.1; also elsewhere on the board
/SpikeAndHoldDriverAndLEDs-16/DriveOut: D46.1 (K), U16.6 (OUT1), U16.7 (OUT2); also elsewhere on the board
/SpikeAndHoldDriverAndLEDs-16/TTLInput: R93.1; also elsewhere on the board
GND: C2.2, C3.1, C4.1, C8.2, C9.1, C10.1, C11.2, C12.1, C13.1, C14.2, C15.1, C16.1, C17.2, C18.1, C19.1, C20.2, C21.1, C22.1, C23.2, C24.1, C25.1, C26.2, C27.1, C28.1, C29.2, C30.1, C31.1, C32.2, C33.1, C34.1, C35.2, C36.1, C37.1, C38.2, C39.1, C40.1, C41.2, C42.1, C43.1, C44.2, C45.1, C46.1, C47.2, C48.1, C49.1, D1.2 (A), D7.2 (A), D10.2 (A), D13.2 (A), D16.2 (A), D19.2 (A), D22.2 (A), D25.2 (A), D28.2 (A), D31.2 (A), D34.2 (A), D37.2 (A), D40.2 (A), D43.2 (A), D46.2 (A), Q1.2 (S), Q3.2 (S), Q4.2 (S), Q5.2 (S), Q6.2 (S), Q7.2 (S), Q8.2 (S), Q9.2 (S), Q10.2 (S), Q11.2 (S), Q12.2 (S), Q13.2 (S), Q14.2 (S), Q15.2 (S), Q16.2 (S), R2.1, R4.1, R5.1, R14.1, R16.1, R17.1, R20.1, R22.1, R23.1, R26.1, R28.1, R29.1, R32.1, R34.1, R35.1, R38.1, R40.1, R41.1, R44.1, R46.1, R47.1, R50.1, R52.1, R53.1, R56.1, R58.1, R59.1, R62.1, R64.1, R65.1, R68.1, R70.1, R71.1, R74.1, R76.1, R77.1, R80.1, R82.1, R83.1, R86.1, R88.1, R89.1, R92.1, R94.1, R95.1, U1.11 (GND), U1.15 (EPAD), U3.11 (GND), U3.15 (EPAD), U4.11 (GND), U4.15 (EPAD), U5.11 (GND), U5.15 (EPAD), U6.11 (GND), U6.15 (EPAD), U7.11 (GND), U7.15 (EPAD), U8.11 (GND), U8.15 (EPAD), U9.11 (GND), U9.15 (EPAD), U10.11 (GND), U10.15 (EPAD), U11.11 (GND), U11.15 (EPAD), U12.11 (GND), U12.15 (EPAD), U13.11 (GND), U13.15 (EPAD), U14.11 (GND), U14.15 (EPAD), U15.11 (GND), U15.15 (EPAD), U16.11 (GND), U16.15 (EPAD); also elsewhere on the board
unnamed: D2.1 (K), R1.1
unnamed: D3.1 (K), R6.1
unnamed: D8.1 (K), R13.1
unnamed: D9.1 (K), R18.1
unnamed: D11.1 (K), R19.1
unnamed: D12.1 (K), R24.1
unnamed: D14.1 (K), R25.1
unnamed: D15.1 (K), R30.1
unnamed: D17.1 (K), R31.1
unnamed: D18.1 (K), R36.1
unnamed: D20.1 (K), R37.1
unnamed: D21.1 (K), R42.1
unnamed: D23.1 (K), R43.1
unnamed: D24.1 (K), R48.1
unnamed: D26.1 (K), R49.1
unnamed: D27.1 (K), R54.1
unnamed: D29.1 (K), R55.1
unnamed: D30.1 (K), R60.1
unnamed: D32.1 (K), R61.1
unnamed: D33.1 (K), R66.1
unnamed: D35.1 (K), R67.1
unnamed: D36.1 (K), R72.1
unnamed: D38.1 (K), R73.1
unnamed: D39.1 (K), R78.1
unnamed: D41.1 (K), R79.1
unnamed: D42.1 (K), R84.1
unnamed: D44.1 (K), R85.1
unnamed: D45.1 (K), R90.1
unnamed: D47.1 (K), R91.1
unnamed: D48.1 (K), R96.1
unnamed: Q1.3 (D), R1.2
unnamed: Q1.1 (G), R3.2, R4.2, U1.14 (INPUT)
unnamed: Q3.3 (D), R13.2
unnamed: Q3.1 (G), R15.2, R16.2, U3.14 (INPUT)
unnamed: Q4.3 (D), R19.2
unnamed: Q4.1 (G), R21.2, R22.2, U4.14 (INPUT)
unnamed: Q5.3 (D), R25.2
unnamed: Q5.1 (G), R27.2, R28.2, U5.14 (INPUT)
unnamed: Q6.3 (D), R31.2
unnamed: Q6.1 (G), R33.2, R34.2, U6.14 (INPUT)
unnamed: Q7.3 (D), R37.2
unnamed: Q7.1 (G), R39.2, R40.2, U7.14 (INPUT)
unnamed: Q8.3 (D), R43.2
unnamed: Q8.1 (G), R45.2, R46.2, U8.14 (INPUT)
unnamed: Q9.3 (D), R49.2
unnamed: Q9.1 (G), R51.2, R52.2, U9.14 (INPUT)
unnamed: Q10.3 (D), R55.2
unnamed: Q10.1 (G), R57.2, R58.2, U10.14 (INPUT)
unnamed: Q11.3 (D), R61.2
unnamed: Q11.1 (G), R63.2, R64.2, U11.14 (INPUT)
unnamed: Q12.3 (D), R67.2
unnamed: Q12.1 (G), R69.2, R70.2, U12.14 (INPUT)
unnamed: Q13.3 (D), R73.2
unnamed: Q13.1 (G), R75.2, R76.2, U13.14 (INPUT)
unnamed: Q14.3 (D), R79.2
unnamed: Q14.1 (G), R81.2, R82.2, U14.14 (INPUT)
unnamed: Q15.3 (D), R85.2
unnamed: Q15.1 (G), R87.2, R88.2, U15.14 (INPUT)
unnamed: Q16.3 (D), R91.2
unnamed: Q16.1 (G), R93.2, R94.2, U16.14 (INPUT)
unnamed: C4.2, U1.5 (BOOT)
unnamed: C3.2, U1.2 (DELAY_ADJ)
unnamed: R2.2, U1.1 (DUTY_CYCLE_ADJ)
unnamed: R5.2, U1.3 (OSC_FREQ_ADJ)
unnamed: R6.2, U1.13 (STATUS_OK_FLAG)
unnamed: C10.2, U3.5 (BOOT)
unnamed: C9.2, U3.2 (DELAY_ADJ)
unnamed: R14.2, U3.1 (DUTY_CYCLE_ADJ)
unnamed: R17.2, U3.3 (OSC_FREQ_ADJ)
unnamed: R18.2, U3.13 (STATUS_OK_FLAG)
unnamed: C13.2, U4.5 (BOOT)
unnamed: C12.2, U4.2 (DELAY_ADJ)
unnamed: R20.2, U4.1 (DUTY_CYCLE_ADJ)
unnamed: R23.2, U4.3 (OSC_FREQ_ADJ)
unnamed: R24.2, U4.13 (STATUS_OK_FLAG)
unnamed: C16.2, U5.5 (BOOT)
unnamed: C15.2, U5.2 (DELAY_ADJ)
unnamed: R26.2, U5.1 (DUTY_CYCLE_ADJ)
unnamed: R29.2, U5.3 (OSC_FREQ_ADJ)
unnamed: R30.2, U5.13 (STATUS_OK_FLAG)
unnamed: C19.2, U6.5 (BOOT)
unnamed: C18.2, U6.2 (DELAY_ADJ)
unnamed: R32.2, U6.1 (DUTY_CYCLE_ADJ)
unnamed: R35.2, U6.3 (OSC_FREQ_ADJ)
unnamed: R36.2, U6.13 (STATUS_OK_FLAG)
unnamed: C22.2, U7.5 (BOOT)
unnamed: C21.2, U7.2 (DELAY_ADJ)
unnamed: R38.2, U7.1 (DUTY_CYCLE_ADJ)
unnamed: R41.2, U7.3 (OSC_FREQ_ADJ)
unnamed: R42.2, U7.13 (STATUS_OK_FLAG)
unnamed: C25.2, U8.5 (BOOT)
unnamed: C24.2, U8.2 (DELAY_ADJ)
unnamed: R44.2, U8.1 (DUTY_CYCLE_ADJ)
unnamed: R47.2, U8.3 (OSC_FREQ_ADJ)
unnamed: R48.2, U8.13 (STATUS_OK_FLAG)
unnamed: C28.2, U9.5 (BOOT)
unnamed: C27.2, U9.2 (DELAY_ADJ)
unnamed: R50.2, U9.1 (DUTY_CYCLE_ADJ)
unnamed: R53.2, U9.3 (OSC_FREQ_ADJ)
unnamed: R54.2, U9.13 (STATUS_OK_FLAG)
unnamed: C31.2, U10.5 (BOOT)
unnamed: C30.2, U10.2 (DELAY_ADJ)
unnamed: R56.2, U10.1 (DUTY_CYCLE_ADJ)
unnamed: R59.2, U10.3 (OSC_FREQ_ADJ)
unnamed: R60.2, U10.13 (STATUS_OK_FLAG)
unnamed: C34.2, U11.5 (BOOT)
unnamed: C33.2, U11.2 (DELAY_ADJ)
unnamed: R62.2, U11.1 (DUTY_CYCLE_ADJ)
unnamed: R65.2, U11.3 (OSC_FREQ_ADJ)
unnamed: R66.2, U11.13 (STATUS_OK_FLAG)
unnamed: C37.2, U12.5 (BOOT)
unnamed: C36.2, U12.2 (DELAY_ADJ)
unnamed: R68.2, U12.1 (DUTY_CYCLE_ADJ)
unnamed: R71.2, U12.3 (OSC_FREQ_ADJ)
unnamed: R72.2, U12.13 (STATUS_OK_FLAG)
unnamed: C40.2, U13.5 (BOOT)
unnamed: C39.2, U13.2 (DELAY_ADJ)
unnamed: R74.2, U13.1 (DUTY_CYCLE_ADJ)
unnamed: R77.2, U13.3 (OSC_FREQ_ADJ)
unnamed: R78.2, U13.13 (STATUS_OK_FLAG)
unnamed: C43.2, U14.5 (BOOT)
unnamed: C42.2, U14.2 (DELAY_ADJ)
unnamed: R80.2, U14.1 (DUTY_CYCLE_ADJ)
unnamed: R83.2, U14.3 (OSC_FREQ_ADJ)
unnamed: R84.2, U14.13 (STATUS_OK_FLAG)
unnamed: C46.2, U15.5 (BOOT)
unnamed: C45.2, U15.2 (DELAY_ADJ)
unnamed: R86.2, U15.1 (DUTY_CYCLE_ADJ)
unnamed: R89.2, U15.3 (OSC_FREQ_ADJ)
unnamed: R90.2, U15.13 (STATUS_OK_FLAG)
unnamed: C49.2, U16.5 (BOOT)
unnamed: C48.2, U16.2 (DELAY_ADJ)
unnamed: R92.2, U16.1 (DUTY_CYCLE_ADJ)
unnamed: R95.2, U16.3 (OSC_FREQ_ADJ)
unnamed: R96.2, U16.13 (STATUS_OK_FLAG)

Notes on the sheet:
2mA
60%
150ms
Float=Master
25kHz
Delay Time = (Cd * 10^6)/1.24
DRIVER6 ACTIVE LIGHT
R_freq = 1 / (1.4518 x 10^−6 + 2.0593 × 10^−7 × F(Hz))

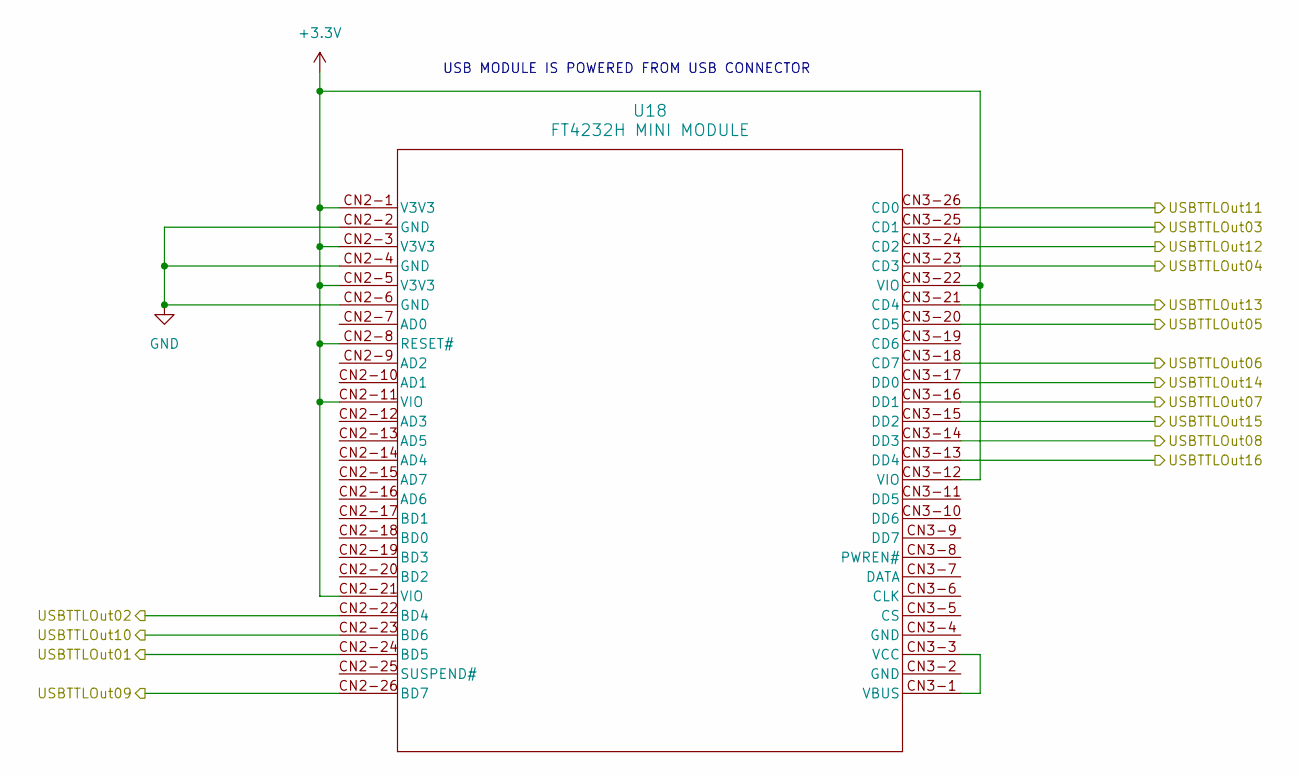
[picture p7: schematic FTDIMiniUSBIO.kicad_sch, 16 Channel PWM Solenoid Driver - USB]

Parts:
U18: FT4232H MINI MODULE; FT4232H_MINI_MODULE

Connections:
+3.3V: U18.CN2-1 (V3V3), U18.CN2-3 (V3V3), U18.CN2-5 (V3V3), U18.CN2-8 (RESET#), U18.CN2-11 (VIO), U18.CN2-21 (VIO), U18.CN3-12 (VIO), U18.CN3-22 (VIO)
/SpikeAndHoldDriverAndLEDs-1/TTLInput: U18.CN2-24 (BD5); also elsewhere on the board
/SpikeAndHoldDriverAndLEDs-2/TTLInput: U18.CN2-22 (BD4); also elsewhere on the board
/SpikeAndHoldDriverAndLEDs-3/TTLInput: U18.CN3-25 (CD1); also elsewhere on the board
/SpikeAndHoldDriverAndLEDs-4/TTLInput: U18.CN3-23 (CD3); also elsewhere on the board
/SpikeAndHoldDriverAndLEDs-5/TTLInput: U18.CN3-20 (CD5); also elsewhere on the board
/SpikeAndHoldDriverAndLEDs-6/TTLInput: U18.CN3-18 (CD7); also elsewhere on the board
/SpikeAndHoldDriverAndLEDs-7/TTLInput: U18.CN3-16 (DD1); also elsewhere on the board
/SpikeAndHoldDriverAndLEDs-8/TTLInput: U18.CN3-14 (DD3); also elsewhere on the board
/SpikeAndHoldDriverAndLEDs-9/TTLInput: U18.CN2-26 (BD7); also elsewhere on the board
/SpikeAndHoldDriverAndLEDs-10/TTLInput: U18.CN2-23 (BD6); also elsewhere on the board
/SpikeAndHoldDriverAndLEDs-11/TTLInput: U18.CN3-26 (CD0); also elsewhere on the board
/SpikeAndHoldDriverAndLEDs-12/TTLInput: U18.CN3-24 (CD2); also elsewhere on the board
/SpikeAndHoldDriverAndLEDs-13/TTLInput: U18.CN3-21 (CD4); also elsewhere on the board
/SpikeAndHoldDriverAndLEDs-14/TTLInput: U18.CN3-17 (DD0); also elsewhere on the board
/SpikeAndHoldDriverAndLEDs-15/TTLInput: U18.CN3-15 (DD2); also elsewhere on the board
/SpikeAndHoldDriverAndLEDs-16/TTLInput: U18.CN3-13 (DD4); also elsewhere on the board
GND: U18.CN2-2 (GND), U18.CN2-4 (GND), U18.CN2-6 (GND); also elsewhere on the board
unnamed: U18.CN3-1 (VBUS), U18.CN3-3 (VCC)

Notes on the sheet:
USB MODULE IS POWERED FROM USB CONNECTOR

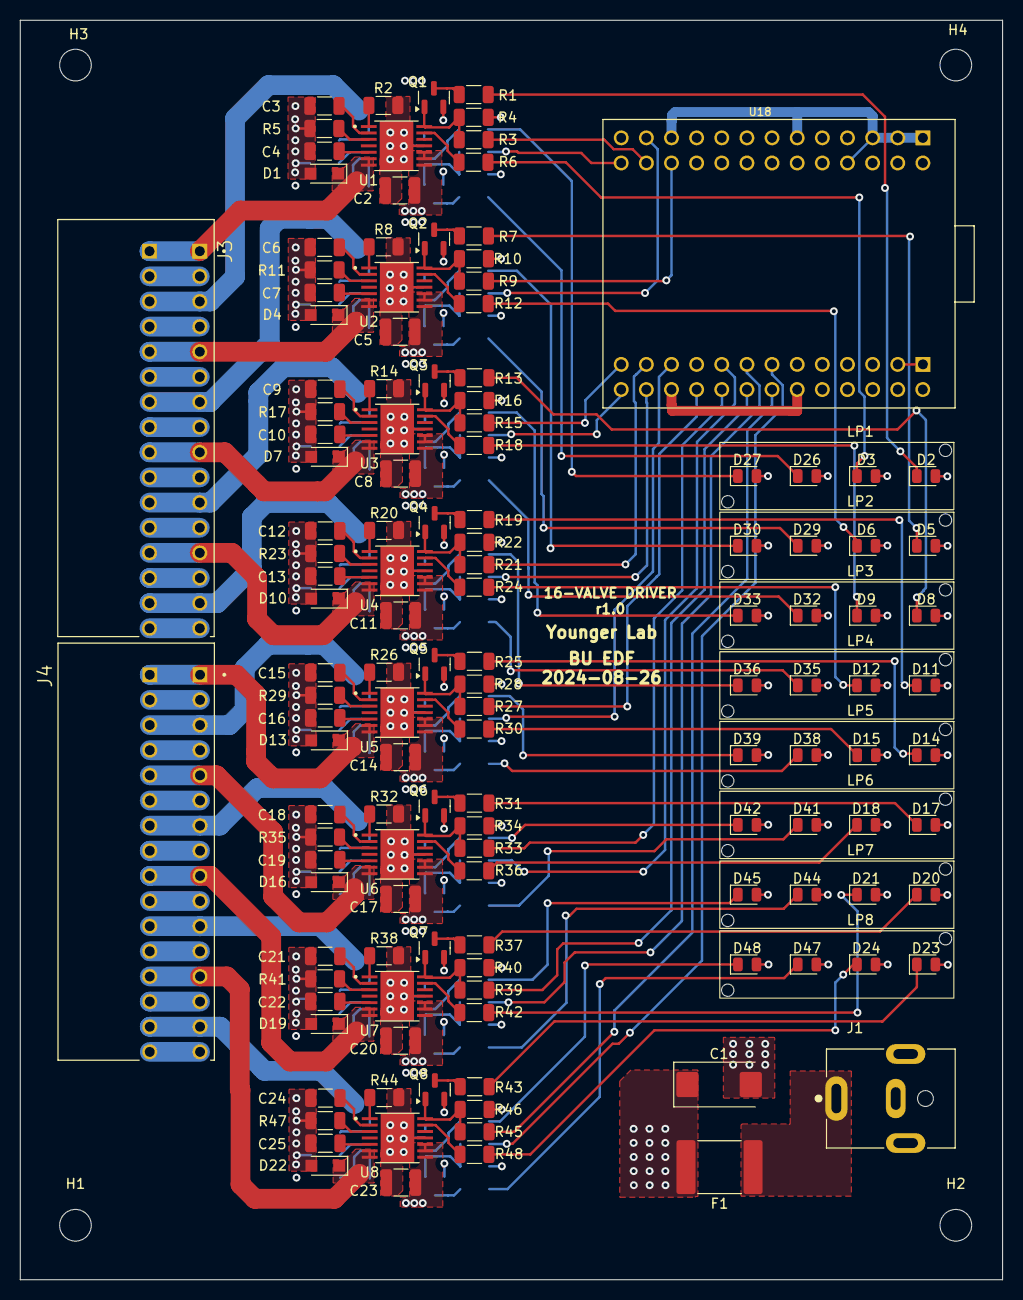
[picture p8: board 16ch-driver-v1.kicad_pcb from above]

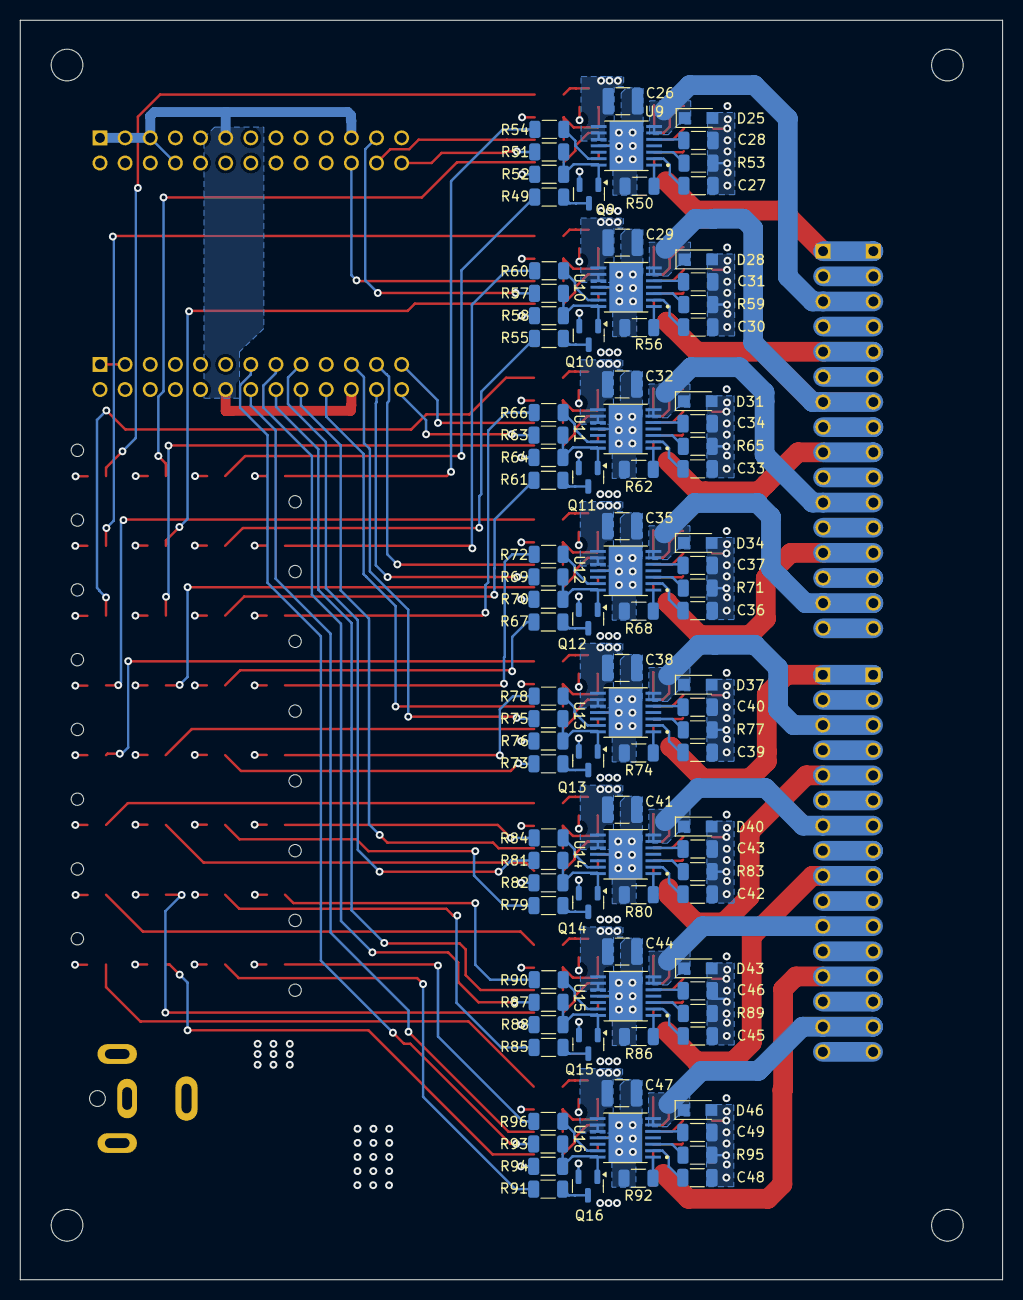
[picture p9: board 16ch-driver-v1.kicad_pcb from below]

Board: 4 copper layers, 99.2 x 127.2 mm, 242 parts (96 on the bottom side), 181 nets.

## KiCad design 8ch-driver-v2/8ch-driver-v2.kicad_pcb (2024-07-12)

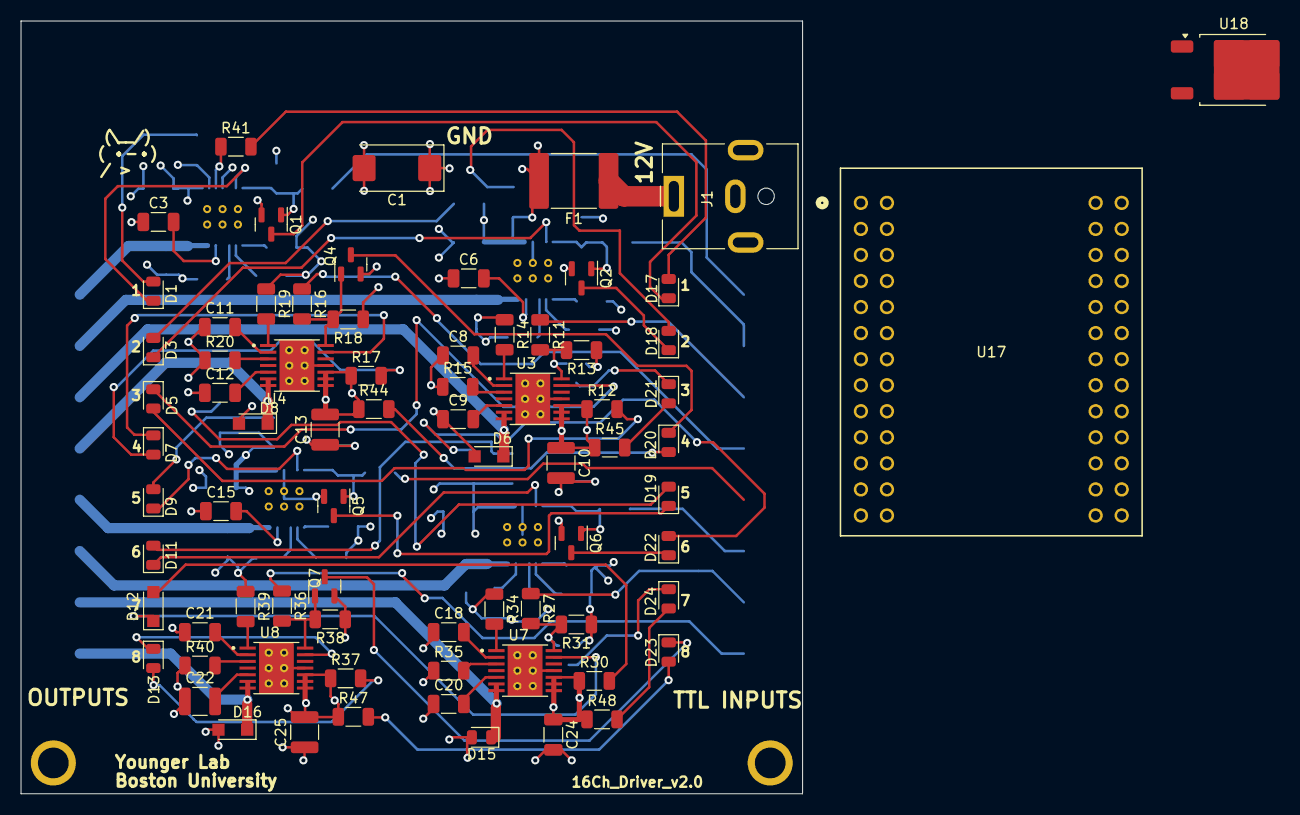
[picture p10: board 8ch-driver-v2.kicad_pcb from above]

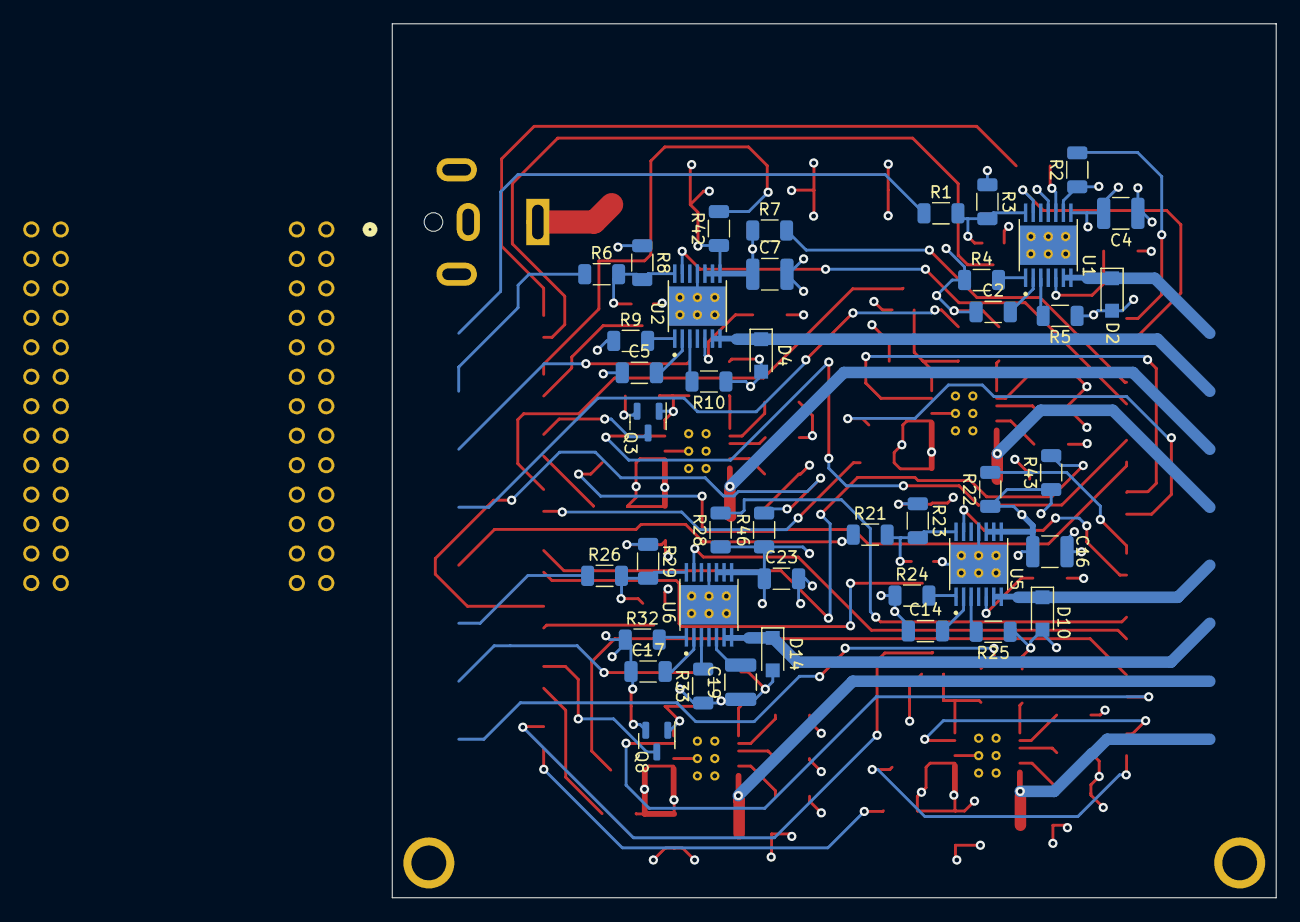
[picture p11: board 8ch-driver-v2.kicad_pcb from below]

Board: 4 copper layers, 76.2 x 75.3 mm, 119 parts (42 on the bottom side), 91 nets.

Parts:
C1: 47uF; CP_EIA-7343-43_Kemet-X_Pad2.25x2.55mm_HandSolder
C2, C5, C8, C11, C14, C17, C20, C23: 0.18uF; C_1206_3216Metric
C3, C6, C9, C12, C15, C18, C21, C24: 470pF; C_1206_3216Metric
C4, C7, C10, C13, C16, C19, C22, C25: 10uF; C_1210_3225Metric
D1, D3, D5, D7, D9, D11, D13, D15: LED; LED_0805_2012Metric
D2, D4, D6, D8, D10, D12, D14, D16: PMEG10010ELRX; Nexperia_CFP3_SOD-123W
D17, D18, D19, D20, D21, D22, D23, D24: LED Green; LED_0805_2012Metric
F1: 0ZCF0125FF2C; Fuse_2920_7451Metric
H1, H2: MountingHole; MountingHole_2.2mm_M2_Pad
J1: Barrel_Jack; BarrelJack_CUI_PJ-063AH_Horizontal
Q1, Q2, Q3, Q4, Q5, Q6, Q7, Q8: 2N7002E; SOT-23
R1, R6, R11, R16, R21, R26, R31, R36: 49R9; R_1206_3216Metric
R2, R3, R7, R8, R12, R13, R17, R18, R22, R23, R27, R28, R32, R33, R37, R38: 4k7; R_1206_3216Metric
R4, R9, R14, R19, R24, R29, R34, R39: 162k; R_1206_3216Metric
R5, R10, R15, R20, R25, R30, R35, R40: 191k; R_1206_3216Metric
R41, R42, R43, R44, R45, R46, R47, R48: 10K; R_1206_3216Metric
U1, U2, U3, U4, U5, U6, U7, U8: DRV104PWP; IC_TPS27S100BPWPR
U17: FT4232H MINI MODULE; FT4232H_FTD
U18: BD33FC0FP; TO-252-2

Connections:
+3.3V: U17.CN2-1 (V3V3), U17.CN2-3 (V3V3), U17.CN2-5 (V3V3), U18.3 (VO)
+12V: C1.1, C4.1, C7.1, C10.1, C13.1, C16.1, C19.1, C22.1, C25.1, F1.2, R2.1, R7.1, R12.1, R17.1, R22.1, R27.1, R32.1, R37.1, R41.1, R42.1, R43.1, R44.1, R45.1, R46.1, R47.1, R48.1, U1.8 (VPS2), U1.9 (VPS1), U1.10 (+VS), U2.8 (VPS2), U2.9 (VPS1), U2.10 (+VS), U3.8 (VPS2), U3.9 (VPS1), U3.10 (+VS), U4.8 (VPS2), U4.9 (VPS1), U4.10 (+VS), U5.8 (VPS2), U5.9 (VPS1), U5.10 (+VS), U6.8 (VPS2), U6.9 (VPS1), U6.10 (+VS), U7.8 (VPS2), U7.9 (VPS1), U7.10 (+VS), U8.8 (VPS2), U8.9 (VPS1), U8.10 (+VS), U18.1 (VCC)
/12V_IN: F1.1, J1.1
/additonal-channels-p1/delay3: C8.2, U3.2 (DELAY_ADJ)
/additonal-channels-p1/delay4: C11.2, U4.2 (DELAY_ADJ)
/additonal-channels-p1/delay5: C14.2, U5.2 (DELAY_ADJ)
/additonal-channels-p1/duty3: R14.2, U3.1 (DUTY_CYCLE_ADJ)
/additonal-channels-p1/duty4: R19.2, U4.1 (DUTY_CYCLE_ADJ)
/additonal-channels-p1/duty5: R24.2, U5.1 (DUTY_CYCLE_ADJ)
/additonal-channels-p1/fault3: D5.1 (K), U3.13 (STATUS_OK_FLAG)
/additonal-channels-p1/fault4: D7.1 (K), U4.13 (STATUS_OK_FLAG)
/additonal-channels-p1/fault5: D9.1 (K), U5.13 (STATUS_OK_FLAG)
/additonal-channels-p1/freq3: R15.2, U3.3 (OSC_FREQ_ADJ)
/additonal-channels-p1/freq4: R20.2, U4.3 (OSC_FREQ_ADJ)
/additonal-channels-p1/freq5: R25.2, U5.3 (OSC_FREQ_ADJ)
/additonal-channels-p1/in_term3: Q3.1 (G), R11.2, R13.2, U3.14 (INPUT)
/additonal-channels-p1/in_term4: Q4.1 (G), R16.2, R18.2, U4.14 (INPUT)
/additonal-channels-p1/in_term5: Q5.1 (G), R21.2, R23.2, U5.14 (INPUT)
/additonal-channels-p2/delay6: C17.2, U6.2 (DELAY_ADJ)
/additonal-channels-p2/delay7: C20.2, U7.2 (DELAY_ADJ)
/additonal-channels-p2/delay8: C23.2, U8.2 (DELAY_ADJ)
/additonal-channels-p2/duty6: R29.2, U6.1 (DUTY_CYCLE_ADJ)
/additonal-channels-p2/duty7: R34.2, U7.1 (DUTY_CYCLE_ADJ)
/additonal-channels-p2/duty8: R39.2, U8.1 (DUTY_CYCLE_ADJ)
/additonal-channels-p2/fault6: D11.1 (K), U6.13 (STATUS_OK_FLAG)
/additonal-channels-p2/fault7: D13.1 (K), U7.13 (STATUS_OK_FLAG)
/additonal-channels-p2/fault8: D15.1 (K), U8.13 (STATUS_OK_FLAG)
/additonal-channels-p2/freq6: R30.2, U6.3 (OSC_FREQ_ADJ)
/additonal-channels-p2/freq7: R35.2, U7.3 (OSC_FREQ_ADJ)
/additonal-channels-p2/freq8: R40.2, U8.3 (OSC_FREQ_ADJ)
/additonal-channels-p2/in_term5: R26.2, R28.2, R31.2, R33.2, R36.2, R38.2, U6.14 (INPUT), U7.14 (INPUT), U8.14 (INPUT)
/delay1: C2.2, U1.2 (DELAY_ADJ)
/delay2: C5.2, U2.2 (DELAY_ADJ)
/duty1: R4.2, U1.1 (DUTY_CYCLE_ADJ)
/duty2: R9.2, U2.1 (DUTY_CYCLE_ADJ)
/fault1: D1.1 (K), U1.13 (STATUS_OK_FLAG)
/fault2: D3.1 (K), U2.13 (STATUS_OK_FLAG)
/freq1: R5.2, U1.3 (OSC_FREQ_ADJ)
/freq2: R10.2, U2.3 (OSC_FREQ_ADJ)
/in_term1: Q1.1 (G), R1.2, R3.2, U1.14 (INPUT)
/in_term2: Q2.1 (G), R6.2, R8.2, U2.14 (INPUT)
GND: C1.2, C2.1, C3.1, C4.2, C5.1, C6.1, C7.2, C8.1, C9.1, C10.2, C11.1, C12.1, C13.2, C14.1, C15.1, C16.2, C17.1, C18.1, C19.2, C20.1, C21.1, C22.2, C23.1, C24.1, C25.2, D2.2 (A), D4.2 (A), D6.2 (A), D8.2 (A), D10.2 (A), D12.2 (A), D14.2 (A), D16.2 (A), J1.2, Q1.2 (S), Q2.2 (S), Q3.2 (S), Q4.2 (S), Q5.2 (S), Q6.2 (S), Q7.2 (S), Q8.2 (S), R3.1, R4.1, R5.1, R8.1, R9.1, R10.1, R13.1, R14.1, R15.1, R18.1, R19.1, R20.1, R23.1, R24.1, R25.1, R28.1, R29.1, R30.1, R33.1, R34.1, R35.1, R38.1, R39.1, R40.1, U1.11 (GND), U1.15 (EPAD), U2.11 (GND), U2.15 (EPAD), U3.11 (GND), U3.15 (EPAD), U4.11 (GND), U4.15 (EPAD), U5.11 (GND), U5.15 (EPAD), U6.11 (GND), U6.15 (EPAD), U7.11 (GND), U7.15 (EPAD), U8.11 (GND), U8.15 (EPAD), U17.CN2-2 (GND), U17.CN2-4 (GND), U17.CN2-6 (GND), U18.2 (GND)
unnamed: D1.2 (A), R2.2
unnamed: D3.2 (A), R7.2
unnamed: D5.2 (A), R12.2
unnamed: D7.2 (A), R17.2
unnamed: D9.2 (A), R22.2
unnamed: D11.2 (A), R27.2
unnamed: D13.2 (A), R32.2
unnamed: D15.2 (A), R37.2
unnamed: D17.2 (A), R41.2
unnamed: D17.1 (K), Q1.3 (D)
unnamed: D18.2 (A), R42.2
unnamed: D18.1 (K), Q2.3 (D)
unnamed: D19.2 (A), R43.2
unnamed: D19.1 (K), Q5.3 (D)
unnamed: D20.2 (A), R44.2
unnamed: D20.1 (K), Q4.3 (D)
unnamed: D21.2 (A), R45.2
unnamed: D21.1 (K), Q3.3 (D)
unnamed: D22.2 (A), R46.2
unnamed: D22.1 (K), Q6.3 (D)
unnamed: D23.2 (A), R47.2
unnamed: D23.1 (K), Q8.3 (D)
unnamed: D24.2 (A), R48.2
unnamed: D24.1 (K), Q7.3 (D)
unnamed: C3.2, U1.5 (BOOT)
unnamed: C6.2, U2.5 (BOOT)
unnamed: C9.2, U3.5 (BOOT)
unnamed: C12.2, U4.5 (BOOT)
unnamed: C15.2, U5.5 (BOOT)
unnamed: C18.2, U6.5 (BOOT)
unnamed: C21.2, U7.5 (BOOT)
unnamed: C24.2, U8.5 (BOOT)
unnamed: U17.CN3-1 (VBUS), U17.CN3-3 (VCC)
Relay01: R1.1, U17.CN2-7 (AD0)
Relay02: R6.1, U17.CN2-10 (AD1)
Relay03: R11.1, U17.CN2-9 (AD2)
Relay04: R16.1, U17.CN2-12 (AD3)
Relay05: R21.1, U17.CN2-14 (AD4)
Relay06: R26.1, U17.CN2-13 (AD5)
Relay07: R31.1, U17.CN2-16 (AD6)
Relay08: R36.1, U17.CN2-15 (AD7)
out01: D2.1 (K), U1.6 (OUT1), U1.7 (OUT2)
out02: D4.1 (K), U2.6 (OUT1), U2.7 (OUT2)
out03: D6.1 (K), U3.6 (OUT1), U3.7 (OUT2)
out04: D8.1 (K), U4.6 (OUT1), U4.7 (OUT2)
out05: D10.1 (K), U5.6 (OUT1), U5.7 (OUT2)
out06: D12.1 (K), U6.6 (OUT1), U6.7 (OUT2)
out07: D14.1 (K), U7.6 (OUT1), U7.7 (OUT2)
out08: D16.1 (K), U8.6 (OUT1), U8.7 (OUT2)

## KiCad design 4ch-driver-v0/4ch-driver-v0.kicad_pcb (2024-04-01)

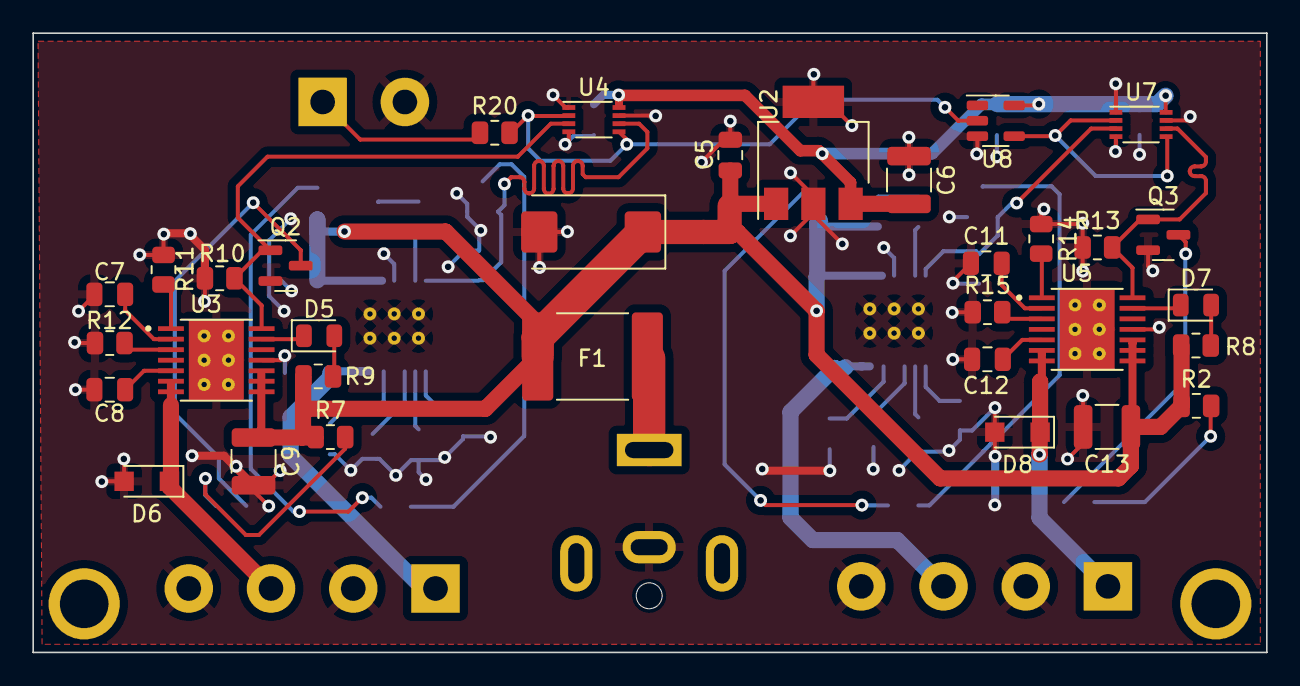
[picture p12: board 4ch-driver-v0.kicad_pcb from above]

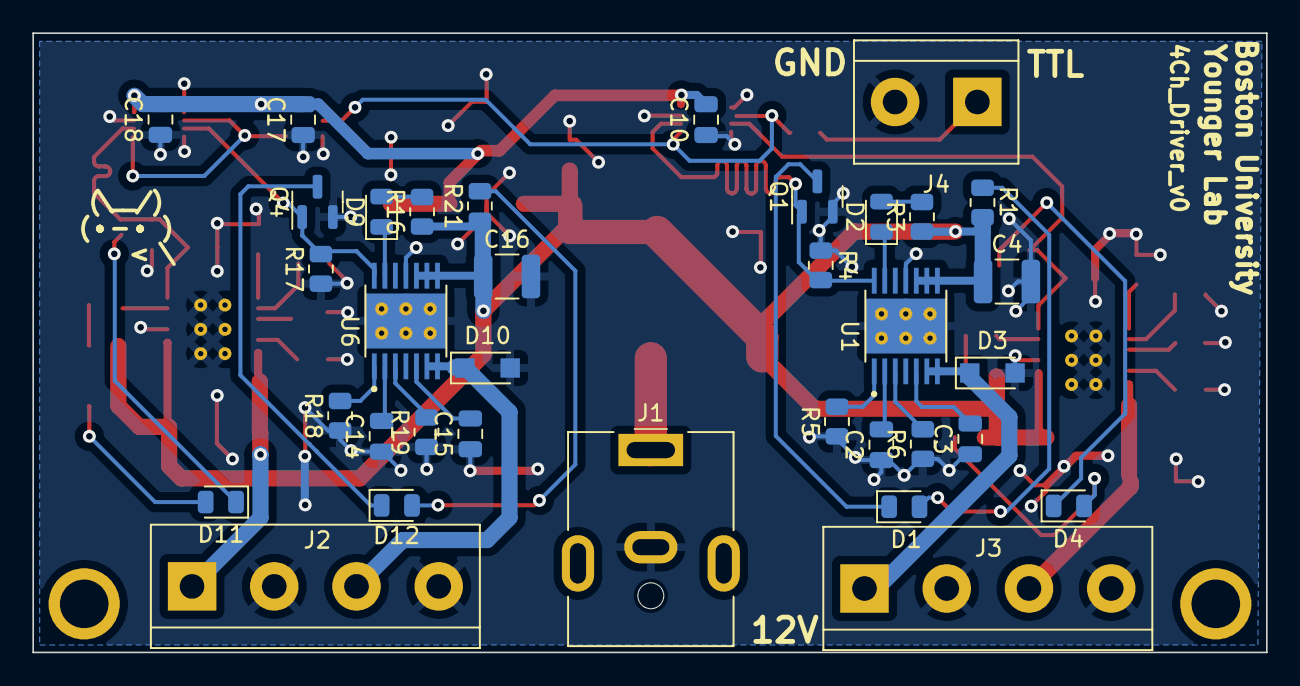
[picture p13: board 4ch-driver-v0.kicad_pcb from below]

Board: 2 copper layers, 76.2 x 38.2 mm, 70 parts (35 on the bottom side), 47 nets.

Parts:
C1: 47uF; CP_EIA-7343-43_Kemet-X_Pad2.25x2.55mm_HandSolder
C2, C7, C11, C14: 0.18uF; C_0805_2012Metric
C3, C8, C12, C15: 470pF; C_0805_2012Metric
C4, C6, C9, C13, C16: 10uF; C_1210_3225Metric
C5, C10, C17, C18: 0.1uF; C_0805_2012Metric
D1, D2, D4, D5, D7, D9, D11, D12: LED; LED_0805_2012Metric
D3, D6, D8, D10: PMEG10010ELRX; Nexperia_CFP3_SOD-123W
F1: 0ZCF0125FF2C; Fuse_2920_7451Metric
H1, H2: MountingHole; MountingHole_2.2mm_M2_Pad
J1: Barrel_Jack; BarrelJack_CUI_PJ-063AH_Horizontal
J2, J3: Screw_Terminal_01x04; TerminalBlock_bornier-4_P5.08mm
J4: Screw_Terminal_01x02; TerminalBlock_bornier-2_P5.08mm
Q1, Q2, Q3, Q4: 2N7002E; SOT-23
R1, R2, R7, R21: 1K; R_0805_2012Metric
R3, R4, R8, R9, R10, R13, R16, R17: 4k7; R_0805_2012Metric
R5, R11, R14, R18: 162k; R_0805_2012Metric
R6, R12, R15, R19: 191k; R_0805_2012Metric
R20: 49R9; R_0805_2012Metric
U1, U3, U5, U6: DRV104PWP; IC_TPS27S100BPWPR
U2: BD750L2FP3-CE2; SOT-223-3_TabPin2
U4, U7: SN74LVC2G125DCUR; VSSOP-8_2.3x2mm_P0.5mm
U8: SN74AHCT1G04DBVR; SOT-23-5

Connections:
+5V: C6.2, C10.2, C17.2, C18.2, U2.3 (Vout), U4.8 (Vcc), U7.8 (Vcc), U8.5 (Vcc)
+12V: C1.1, C4.1, C5.2, C9.1, C13.1, C16.1, F1.2, R1.1, R2.1, R3.1, R7.1, R8.1, R9.1, R16.1, R21.1, U1.8 (VPS2), U1.9 (VPS1), U1.10 (+VS), U2.1 (Vcc), U3.8 (VPS2), U3.9 (VPS1), U3.10 (+VS), U5.8 (VPS2), U5.9 (VPS1), U5.10 (+VS), U6.8 (VPS2), U6.9 (VPS1), U6.10 (+VS)
/12V_IN: F1.1, J1.1
/delay1: C2.2, U1.2 (DELAY_ADJ)
/delay2: C7.2, U3.2 (DELAY_ADJ)
/duty1: R5.2, U1.1 (DUTY_CYCLE_ADJ)
/duty2: R11.2, U3.1 (DUTY_CYCLE_ADJ)
/fault1: D2.1 (K), U1.13 (STATUS_OK_FLAG)
/fault2: D5.1 (K), U3.13 (STATUS_OK_FLAG)
/freq1: R6.2, U1.3 (OSC_FREQ_ADJ)
/freq2: R12.2, U3.3 (OSC_FREQ_ADJ)
/in: J4.1, R20.1
/in_term1: Q1.1 (G), R4.2, U1.14 (INPUT), U4.6 (1Y)
/in_term2: Q2.1 (G), R10.2, U3.14 (INPUT), U4.3 (2Y)
/inverted_signal/delay3: C11.2, U5.2 (DELAY_ADJ)
/inverted_signal/delay4: C14.2, U6.2 (DELAY_ADJ)
/inverted_signal/duty3: R14.2, U5.1 (DUTY_CYCLE_ADJ)
/inverted_signal/duty4: R18.2, U6.1 (DUTY_CYCLE_ADJ)
/inverted_signal/fault3: D7.1 (K), U5.13 (STATUS_OK_FLAG)
/inverted_signal/fault4: D9.1 (K), U6.13 (STATUS_OK_FLAG)
/inverted_signal/freq3: R15.2, U5.3 (OSC_FREQ_ADJ)
/inverted_signal/freq4: R19.2, U6.3 (OSC_FREQ_ADJ)
/inverted_signal/in_term3: Q3.1 (G), R13.2, U5.14 (INPUT), U7.6 (1Y)
/inverted_signal/in_term4: Q4.1 (G), R17.2, U6.14 (INPUT), U7.3 (2Y)
/inverted_signal/inverted: U7.2 (1A), U7.5 (2A), U8.4 (Out)
/inverted_signal/out3: D8.1 (K), J2.1, U5.6 (OUT1), U5.7 (OUT2)
/inverted_signal/out4: D10.1 (K), J2.3, U6.6 (OUT1), U6.7 (OUT2)
/out1: D3.1 (K), J3.1, U1.6 (OUT1), U1.7 (OUT2)
/out2: D6.1 (K), J3.3, U3.6 (OUT1), U3.7 (OUT2)
GND: C1.2, C2.1, C3.1, C4.2, C5.1, C6.1, C7.1, C8.1, C9.2, C10.1, C11.1, C12.1, C13.2, C14.1, C15.1, C16.2, C17.1, C18.1, D3.2 (A), D6.2 (A), D8.2 (A), D10.2 (A), J1.2, J2.2, J2.4, J3.2, J3.4, J4.2, Q1.2 (S), Q2.2 (S), Q3.2 (S), Q4.2 (S), R4.1, R5.1, R6.1, R10.1, R11.1, R12.1, R13.1, R14.1, R15.1, R17.1, R18.1, R19.1, U1.11 (GND), U1.15 (EPAD), U1.16, U1.17, U1.18, U1.19, U1.20, U1.21, U2.2 (GND), U3.11 (GND), U3.15 (EPAD), U3.16, U3.17, U3.18, U3.19, U3.20, U3.21, U4.1 (1~OE), U4.4 (GND), U4.7 (2~OE), U5.11 (GND), U5.15 (EPAD), U5.16, U5.17, U5.18, U5.19, U5.20, U5.21, U6.11 (GND), U6.15 (EPAD), U6.16, U6.17, U6.18, U6.19, U6.20, U6.21, U7.1 (1~OE), U7.4 (GND), U7.7 (2~OE), U8.3 (GND)
unnamed: D1.2 (A), R1.2
unnamed: D1.1 (K), Q1.3 (D)
unnamed: D2.2 (A), R3.2
unnamed: D4.2 (A), R7.2
unnamed: D4.1 (K), Q2.3 (D)
unnamed: D5.2 (A), R9.2
unnamed: D7.2 (A), R8.2
unnamed: D9.2 (A), R16.2
unnamed: D11.2 (A), R2.2
unnamed: D11.1 (K), Q3.3 (D)
unnamed: D12.2 (A), R21.2
unnamed: D12.1 (K), Q4.3 (D)
unnamed: C3.2, U1.5 (BOOT)
unnamed: C8.2, U3.5 (BOOT)
unnamed: C12.2, U5.5 (BOOT)
unnamed: C15.2, U6.5 (BOOT)
in_sig: R20.2, U4.2 (1A), U4.5 (2A), U8.2 (In)

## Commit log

2023-09-02 creation of 8ch-v0 and 2ch-v0
    [2ch-driver-v0-BOM.csv, 2ch-driver-v0.kicad_pcb, 2ch-driver-v0.kicad_sch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]
2023-12-13 Revised Board
    [8ch-driver-v1.1.kicad_pcb, 8ch-driver-v1.1.kicad_sch, additonal-channels-p1.kicad_sch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]
2024-04-01 Added design files for 4-ch opposing dir board
    [4ch-driver-v0-BOM.csv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]
2024-04-01 fixed screw terminal side
    [4ch-driver-v0-B_Cu.gbr, 4ch-driver-v0-B_Mask.gbr, 4ch-driver-v0-B_Paste.gbr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]
2024-06-06 Cleaning up the protoboard
    Moving away from screw terminals in V2.
    [8ch-driver-v2.kicad_pcb, 8ch-driver-v2.kicad_sch, additonal-channels-p1.kicad_sch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]
2024-06-13 added 8 more channels and an FTDH chip
    [8ch-driver-v2.kicad_sch, FTDIMiniUSBIO.kicad_sch, additional-channels-12-14.kicad_sch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]
2024-07-12 mucho mas progresso
    [16ch-driver-v1.kicad_pcb, 16ch-driver-v1.kicad_sch, 8ch-driver-v2.kicad_pcb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]
2024-08-26 16-valve PCB layout for inspection
    [16ch-driver-v1.kicad_pcb, 16ch-driver-v1.kicad_sch, CUI_DEVICES_PJ-063AH.step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]
2024-08-27 Gerber File Creation
    [16ch-driver-v1-B_Cu.gbr, 16ch-driver-v1-B_Mask.gbr, 16ch-driver-v1-B_Paste.gbr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]
2024-09-04 Larger Board and DRC Cleanup
    [16ch-driver-v1-B_Cu.gbr, 16ch-driver-v1-B_Mask.gbr, 16ch-driver-v1-B_Paste.gbr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]
2024-09-04 Clean DRC!!
    [16ch-driver-v1-B_Cu.gbr, 16ch-driver-v1-B_Mask.gbr, 16ch-driver-v1-B_Paste.gbr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]
2024-09-11 Final Files for Production
    [16ch-driver-v1-B_Cu.gbr, 16ch-driver-v1-B_Mask.gbr, 16ch-driver-v1-B_Paste.gbr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]
2024-10-06 zipped for pcbfab
